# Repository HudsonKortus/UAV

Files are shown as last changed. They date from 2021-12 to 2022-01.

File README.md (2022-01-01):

<div align="center">
    accessibility text
</div>

# UAV 2.0
UAV 2.0 is a thrust vector controlled, electric ducted fan powered UAV. I started this project in June of 2020, and have been working on it off and on ever since. Over the course of this project I have become a better programmer, more confident in CAD, I have learned how to aerodynamically simulate parts in CFD, and taught myself how to make custom PCBs using EAGLE. There is still work that needs to be done to get the UAV to a place where it can fly. 

# ABOUT
The UAV utilizes moveable thrust vanes which are in the exhaust stream of the electric ducted fan to stabilize the vehicle. The control system is a very basic PID loop, but I plan to move to an LQG controller which will allow the UAV to hover in one place. All the electronics are custom. I used a Teensy 4.0 for the microcontroller, and BMI 088 for the gyroscope and acceleration reading. The electric ducted fan is a basic one I got off Amazon which runs off a 4s, 4000mAh lipo. The electric ducted fan produces a little over 1.2kg of static thrust which currently is not enough to lift the vehicle.

# TODO
 * make UAV be tethered to battery instead of carrying it because the battery is too heavy
 * change form using thrust vanes to gimbaling the motor because thrust vanes cannot be practically mathematically characterizes
 * rewrite code to be more object oriented
 * replace the PID controller with an LQG controller
 * make FAA compliant

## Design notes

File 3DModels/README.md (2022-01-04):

# EDF Mount
<div align="float left">
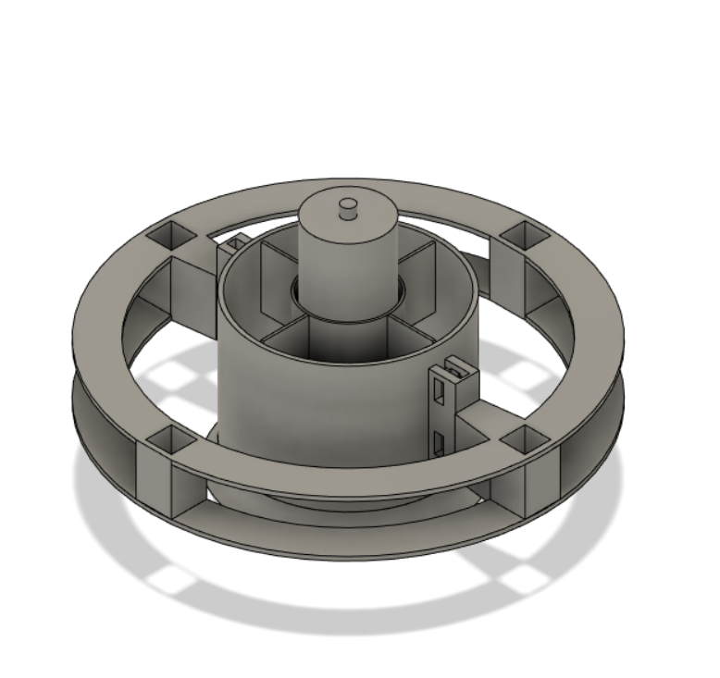
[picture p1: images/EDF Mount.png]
  
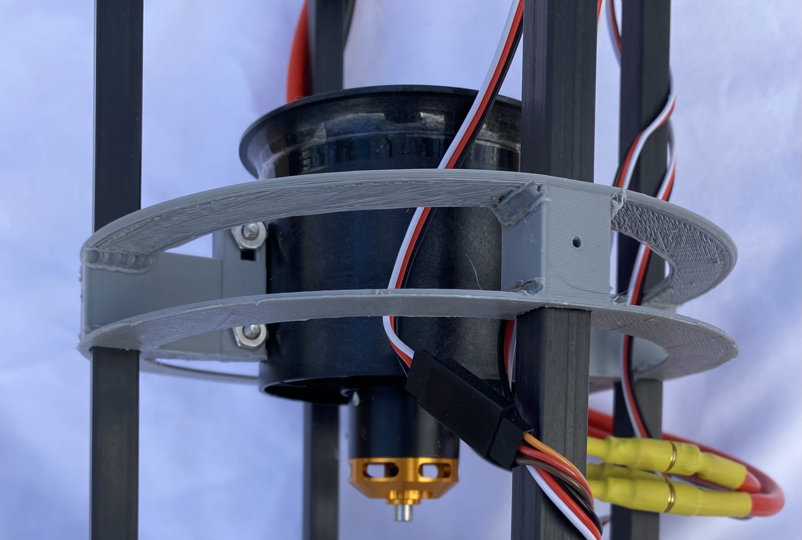
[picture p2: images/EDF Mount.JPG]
  
</div>
This part mounts the electric ducted fan to the carbon fiber frame. I designed this part to be as light as possible which is why there are only 2 thin strips of material connecting each of the frame attachment points. The mount does not need to be rigid in the vertical axis, and just needs to transfer the lift generated by the electric ducted fan to the carbon fiber frame, while ensuring it is rigid horizontally. From my testing, I found that it was unnecessary to have all 4 frame attachment points be fixed to the electric ducted fan, so instead, I only attached the electric ducted fan to 2 of the frame mounting points.

<br/>

# Electronics Disk Mount
<div align="float left">
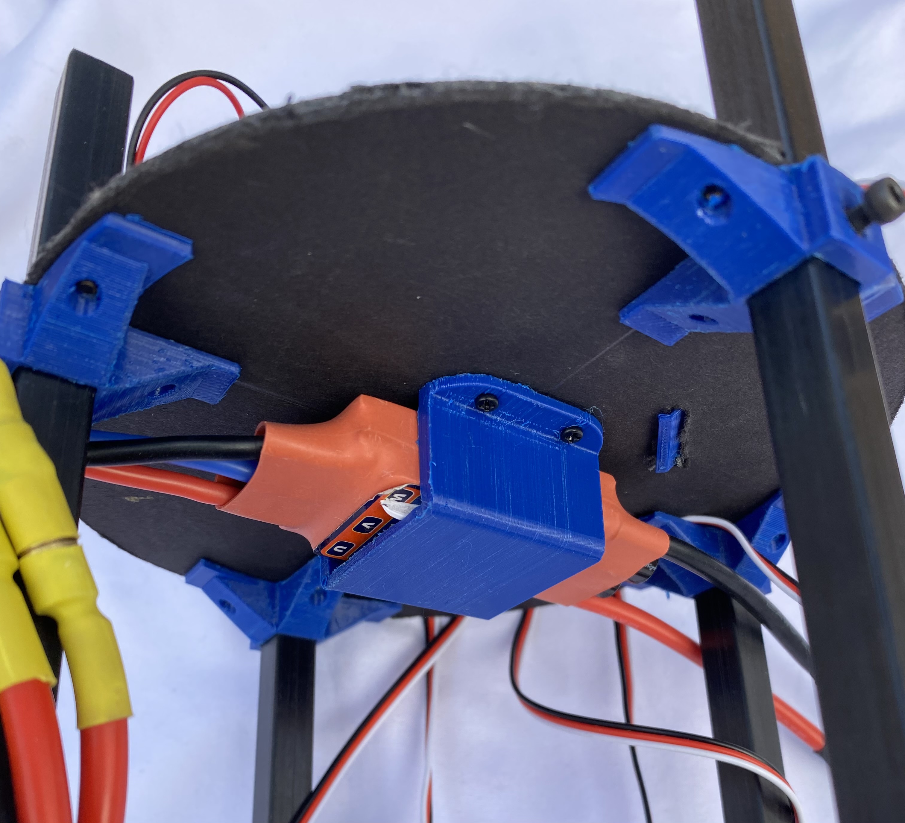
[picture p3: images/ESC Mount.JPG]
  
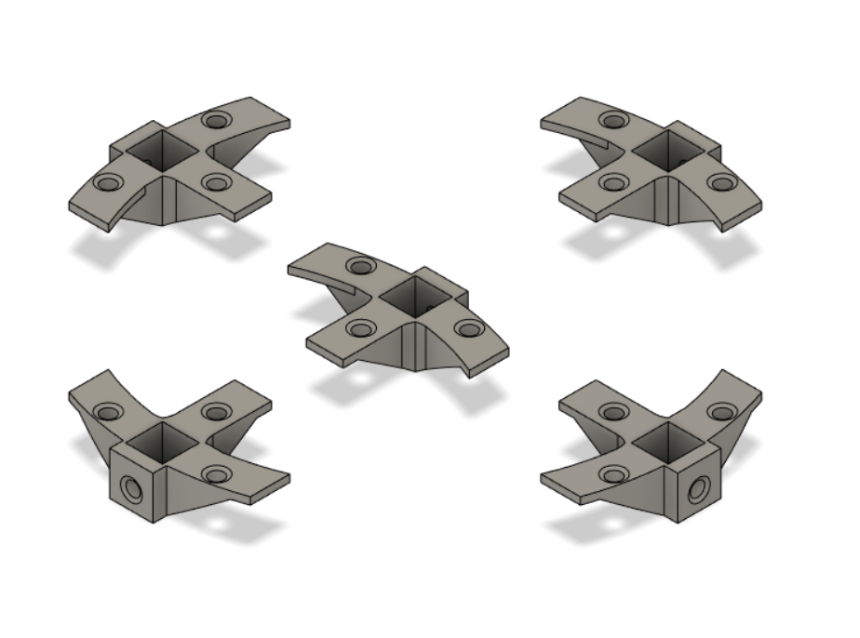
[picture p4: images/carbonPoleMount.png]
  
</div>
 This part is used to affix the foam core disk for the electronics to the carbon fiber mount. The round holes are designed to have threaded inserts mounted in them to allow the foam disk to be screwed in, and to allow the mounts to be screwed to the carbon fiber frame. This file contains all 4 mounts arranged radially and ready to be mounted, as well as a single one which will be easier to 3d print, change, or look at.

<br/>

# ESC Mount
<div align="float left">
  
</div>
This part mounts the 80A ESC to the bottom of the foam core electronics disk. This part is screwed into the foam board with m2 screws.

<br/>

# Gimbal Mount
<div align="float left">
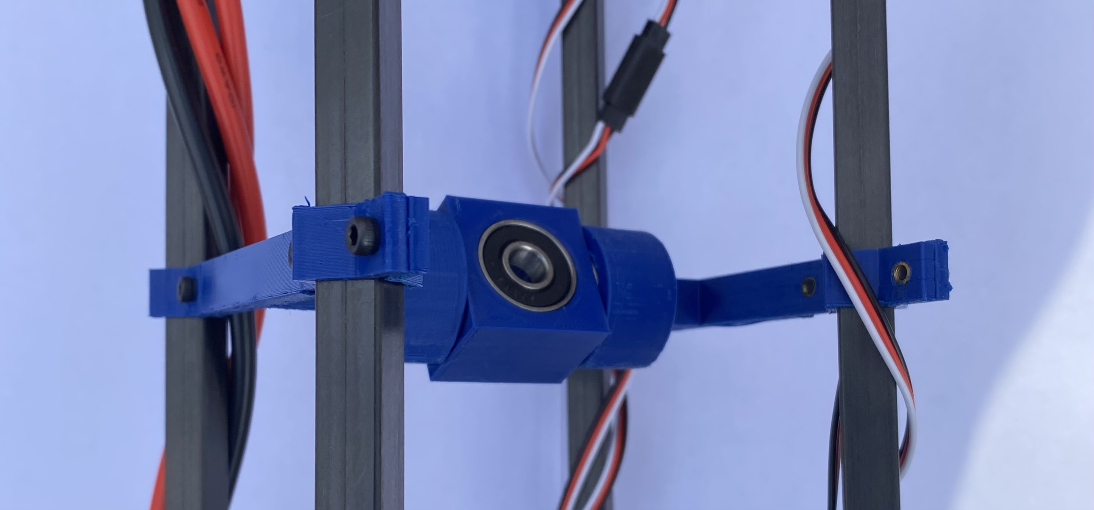
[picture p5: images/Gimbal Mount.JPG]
  
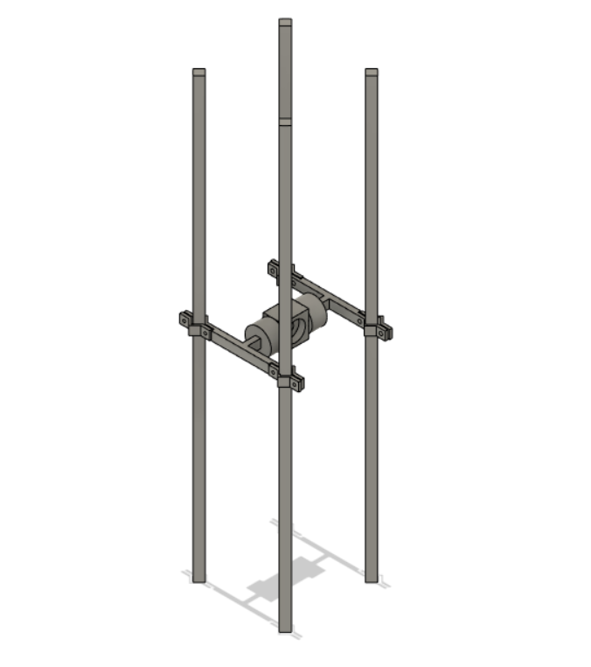
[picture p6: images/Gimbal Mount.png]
  
</div>
This is a two degree of freedom gimbal to allow for the uav to be stationary mounted and tested. It uses threaded inserts and m3 screws to clamp itself to the frame.

<br/>

# Servo Mount
<div align="float left">
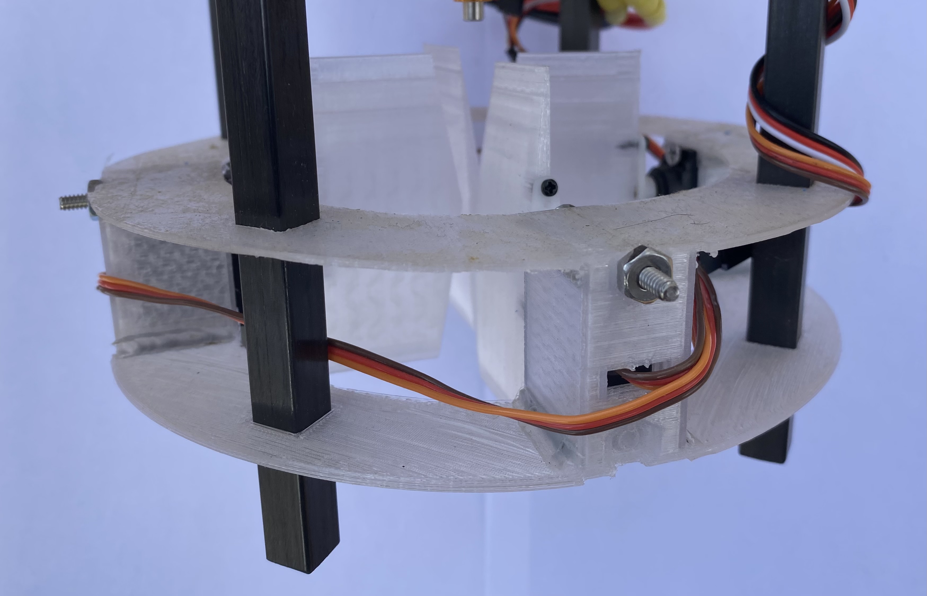
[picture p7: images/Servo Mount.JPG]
  
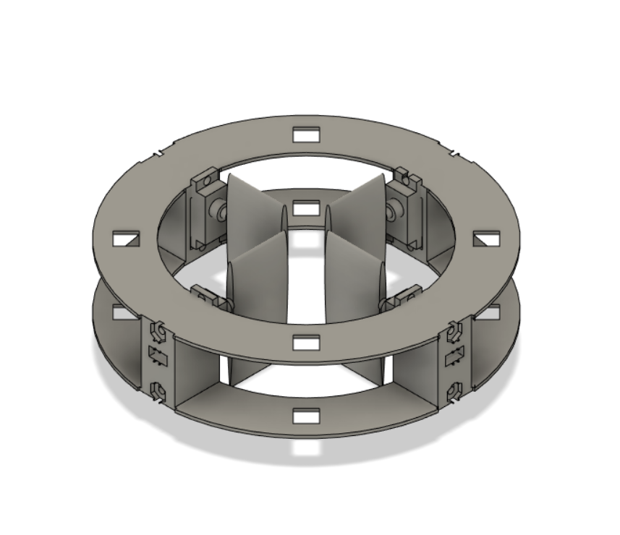
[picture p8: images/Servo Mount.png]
  
</div>
This mounts the servos and thrust vanes to the carbon fiber frame. This part is also extremely optimized to keep the weight down as much as possible.

<br/>

# Thrust Vane
<div align="float left">
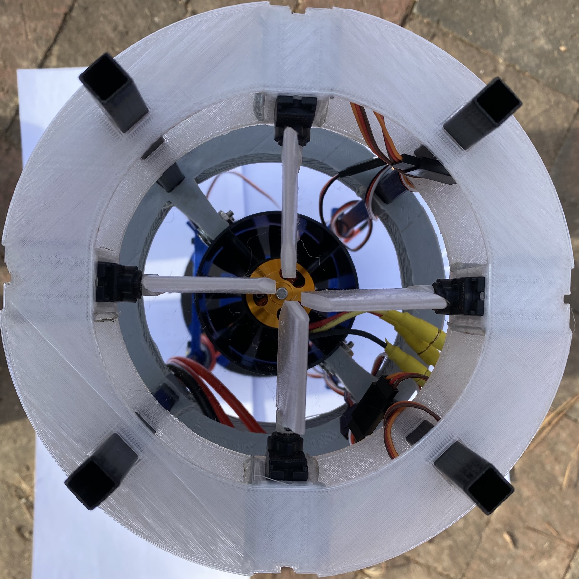
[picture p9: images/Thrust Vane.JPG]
  
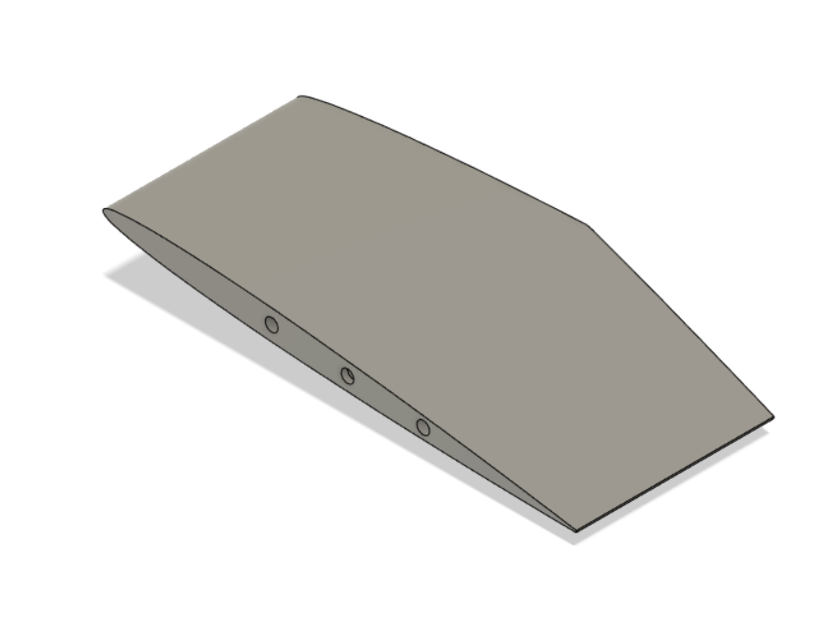
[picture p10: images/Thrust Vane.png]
  
</div>
Thrust vane used to control the UAV.

<br/>

# UAV PCB
<div align="float left">
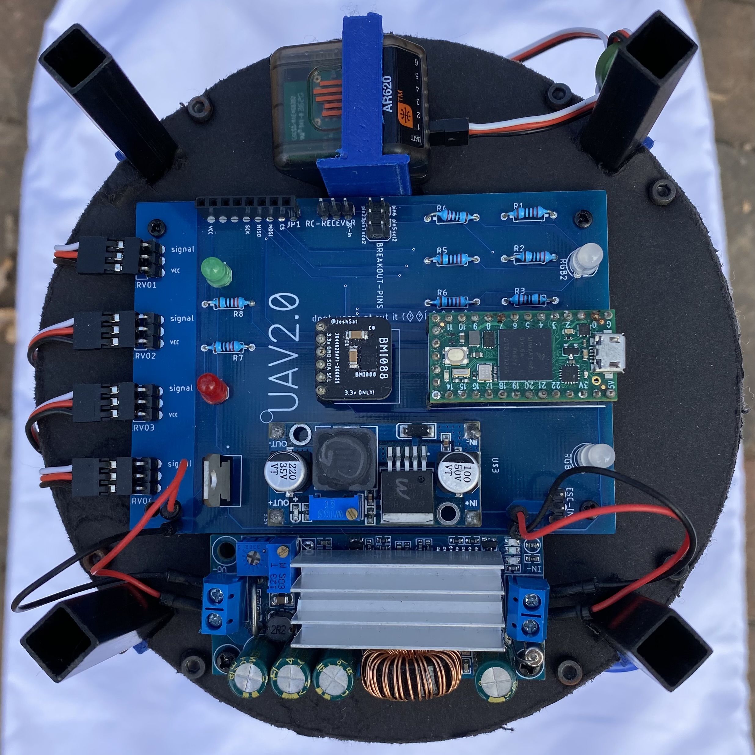
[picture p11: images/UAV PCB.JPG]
  
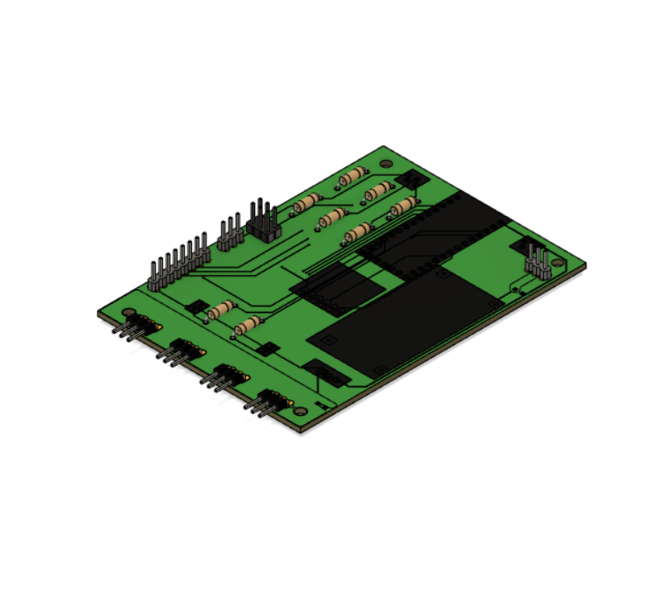
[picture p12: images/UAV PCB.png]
  
</div>
All the necessary data for the PCB used on my UAV is here. Inside the UAV PEB folder is the schematic and board as well as a zip containing all the pertinent information for the PCB to be manufactured.

<br/>

# Receiver Mount
<div align="float left">
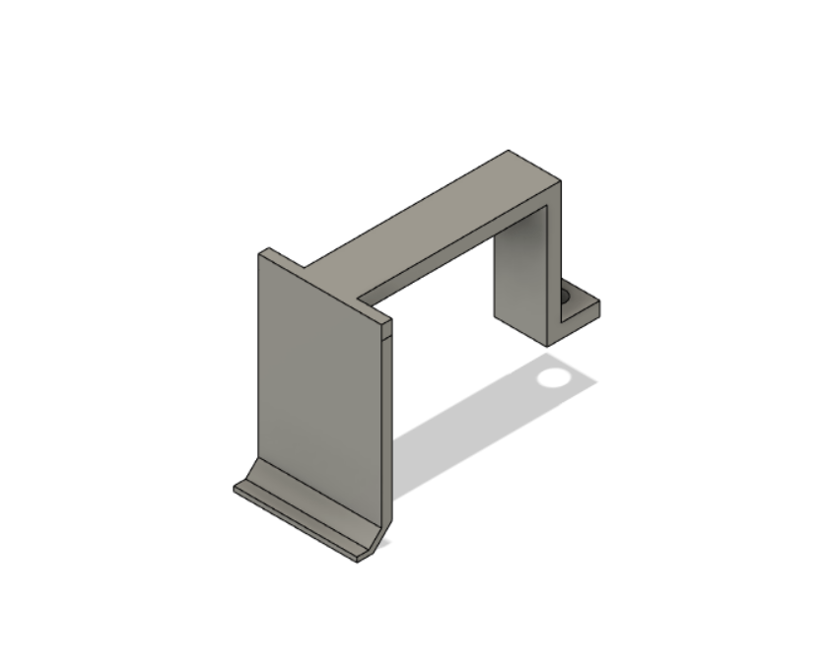
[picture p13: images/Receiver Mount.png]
  
</div>
Mounts the RC receiver to the foam core.

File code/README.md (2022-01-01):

# About
This is the code which runs the UAV. It uses a simple PID loop to determine the amount of torque required to keep the vehicle under control, In order to account for the thrust of the electric ducted fan, I used an equation which calculates the thrust generated by a thrust vane as detailed in <a href="https://smartech.gatech.edu/handle/1853/59935">this paper by Jacob Grey Sobering</a>. Quaternions are used to derive the orientation of the UAV from acceleration measurements. I used a closed source quaternion library, so that code is missing from this repository. If you want to use this code, simply add your own orientation code to the angle_output method. This code is over a year old and since writing it, I have greatly improved in my programming abilities. I will soon rewrite the code to be truly object oriented, more compact, and easier to read.

# TODO
 * rewrite code to be more object oriented
 * replace the PID controller with an LQG controller

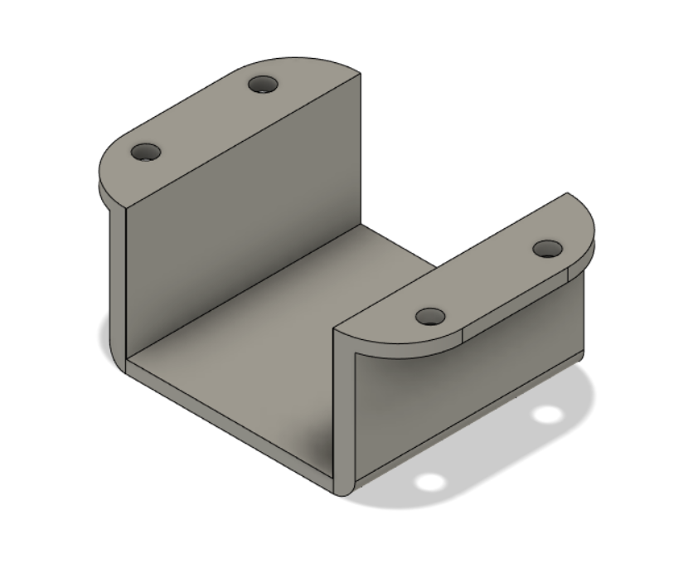
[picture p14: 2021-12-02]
images/ESC Mount.png

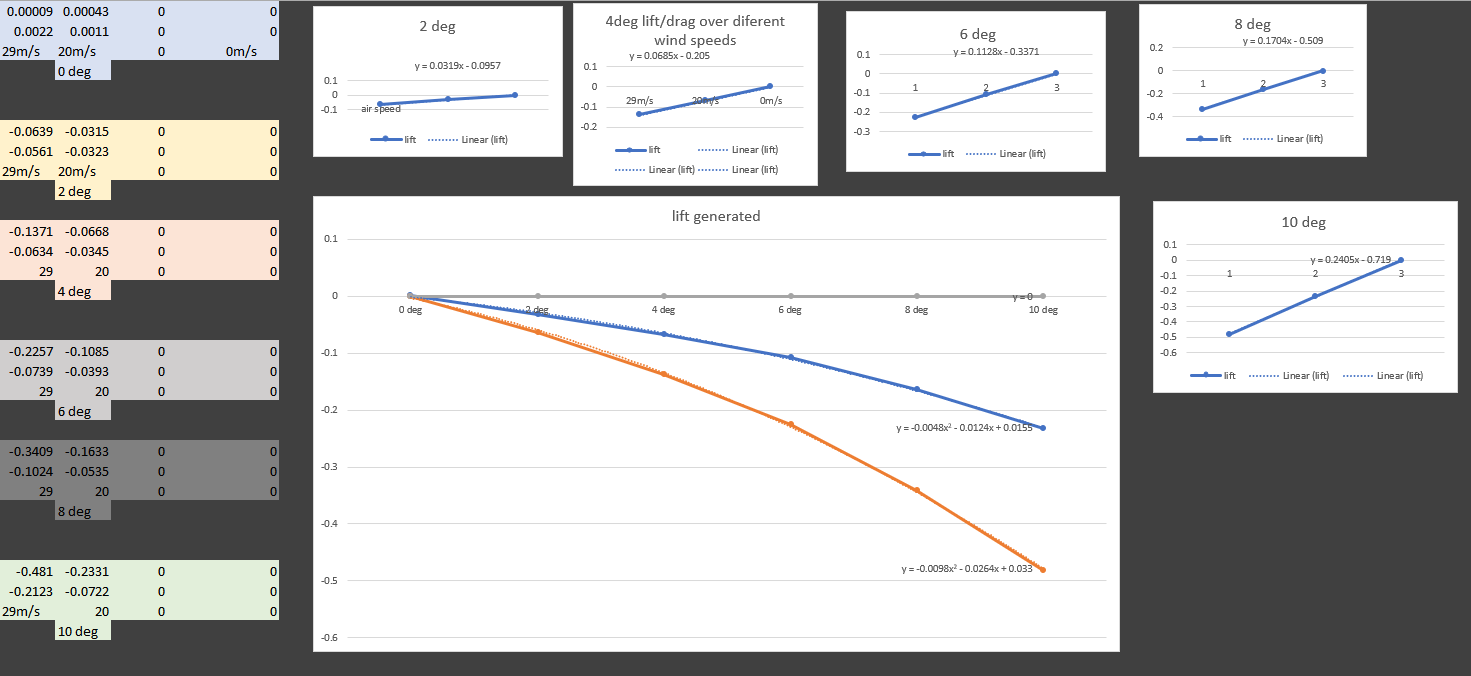
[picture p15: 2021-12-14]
images/Thrust Vane Data.JPG

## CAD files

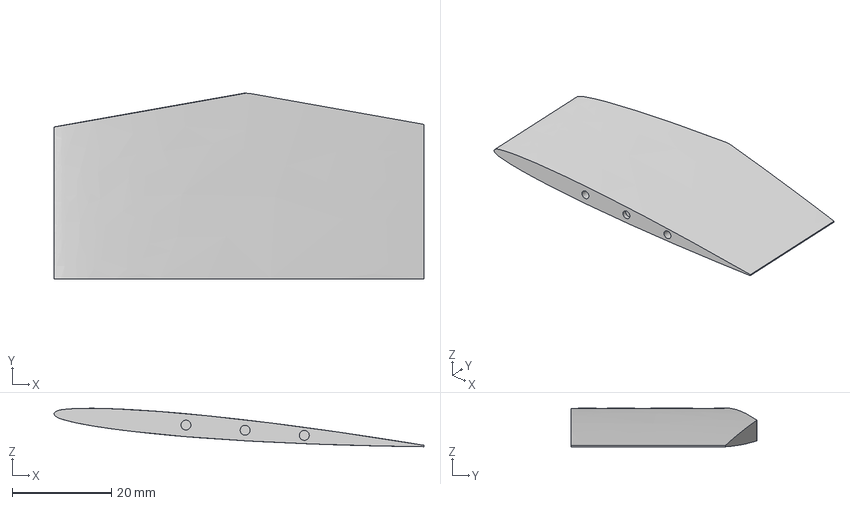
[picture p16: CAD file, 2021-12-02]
3DModels/thrustVane.step
74.7 x 37.5 x 7.78 mm

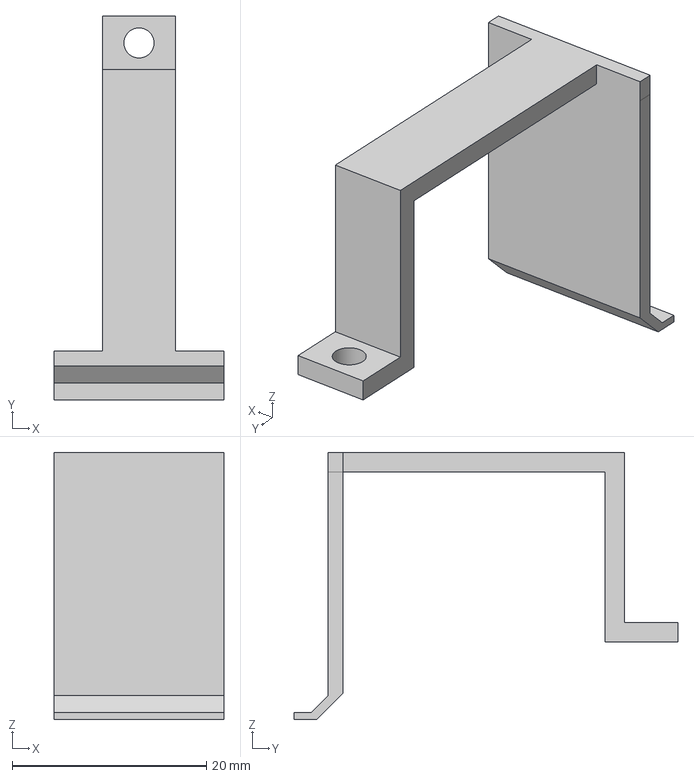
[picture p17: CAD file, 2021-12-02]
3DModels/receverClamp.step
17.5 x 39.5 x 27.5 mm

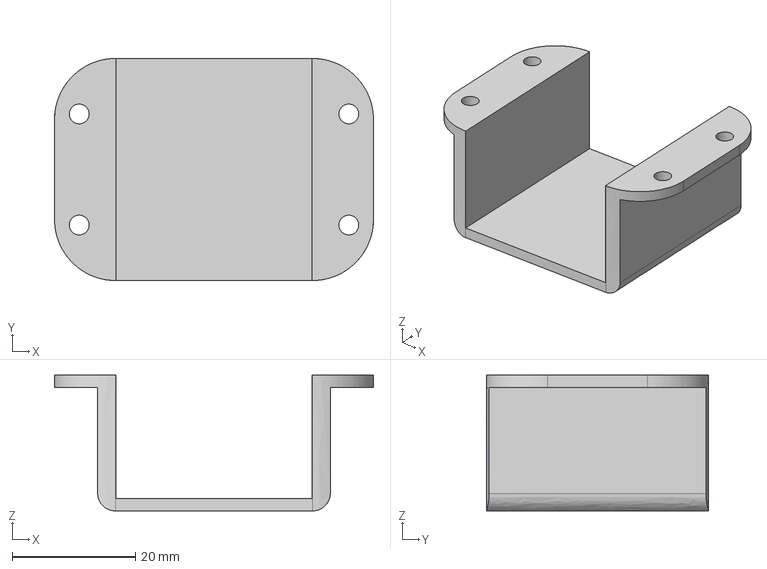
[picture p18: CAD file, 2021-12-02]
3DModels/ESCHolder.step
51.7 x 36.0 x 22.0 mm

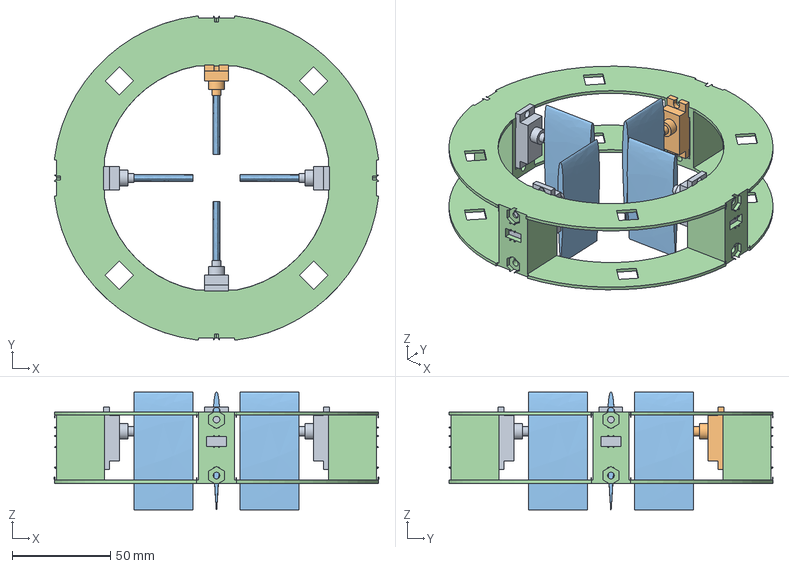
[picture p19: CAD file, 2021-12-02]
3DModels/servoMount.step
165.1 x 165.0 x 60.0 mm
UAVservo v4
thrust vane

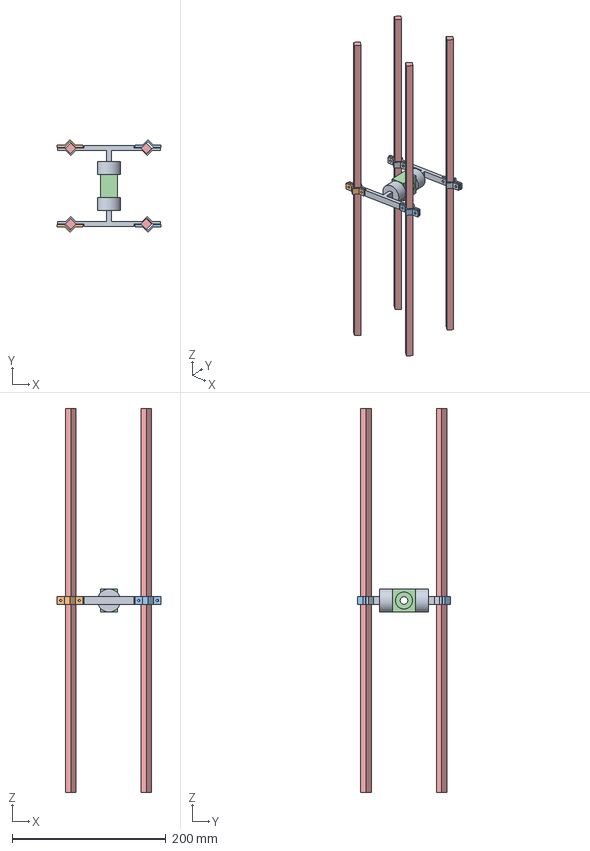
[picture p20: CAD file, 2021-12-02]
3DModels/gimbalForUAV.step
135.8 x 120.6 x 500.0 mm
primary
secondary
main box
CarbonPoles2

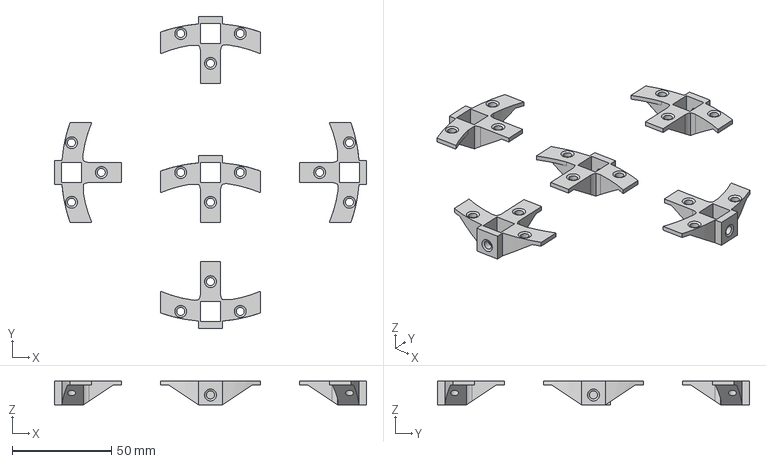
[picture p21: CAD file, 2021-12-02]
3DModels/carbonPoleMount.step
157.2 x 157.2 x 12.0 mm
mount singe x 5

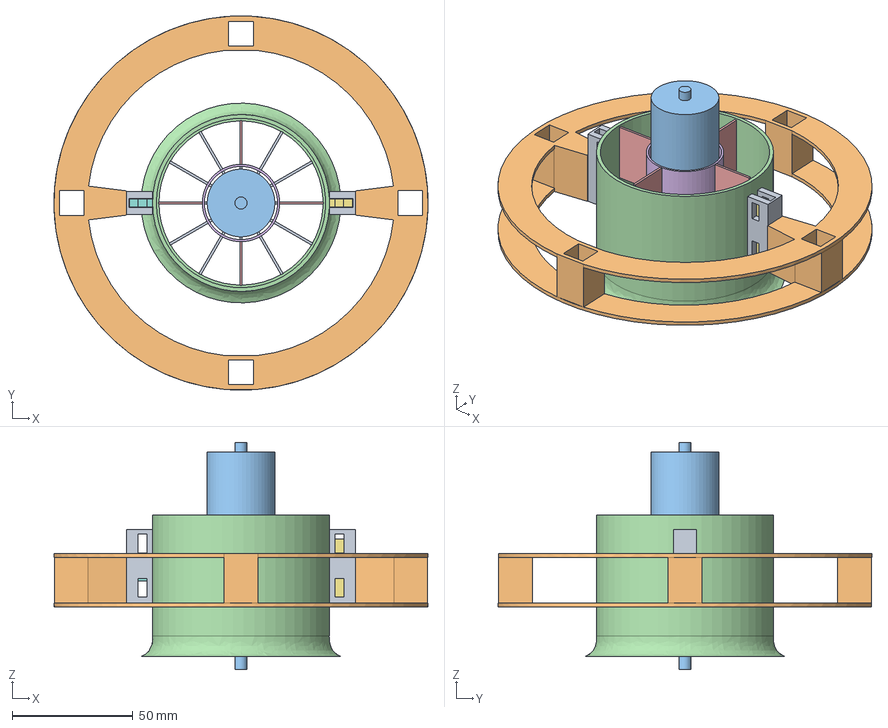
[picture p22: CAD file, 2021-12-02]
3DModels/EDFholder.step
154.6 x 154.6 x 94.0 mm
edfclamp x 2
EDFholder
motor
shroud
blades

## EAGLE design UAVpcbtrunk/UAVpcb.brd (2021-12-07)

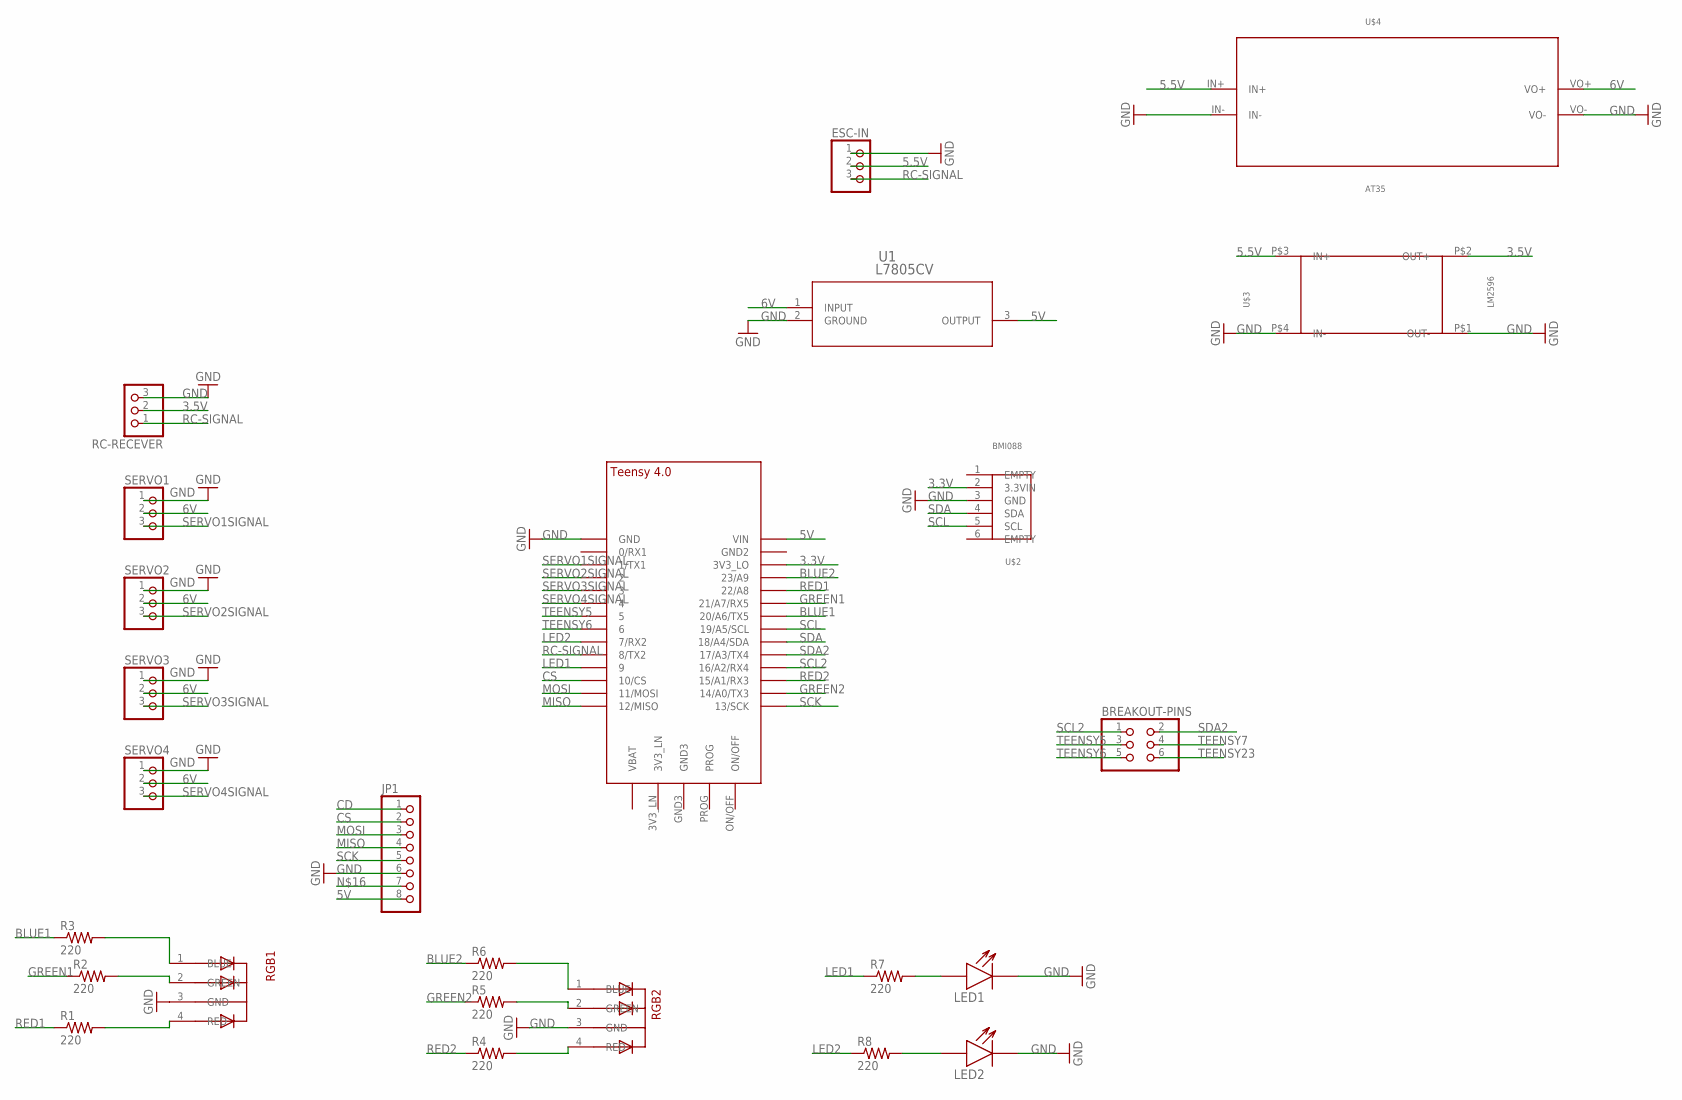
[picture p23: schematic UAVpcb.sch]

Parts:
BREAKOUT-PINS: PINHD-2X3; 2X03
ESC-IN: PINHD-1X3; 1X03
JP1: PINHD-1X8; 1X08
LED1, LED2: LED2P; JP1
R1, R2, R3, R4, R5, R6, R7, R8: 220; 0207/10
RC-RECEVER: PINHD-1X3; 1X03
RGB1, RGB2: 5MMRGBLED; LED5MMRGB
SERVO1, SERVO2, SERVO3, SERVO4: PINHD-1X3/90; 1X03/90
U1: L7805CV; TO-220_STM
U$1: TEENSY_4.0
U$2: BMI088; 1X06
U$3: LM2596
U$4: AT35

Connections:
3.3V: U$1.3V3_LO, U$2.2 (3.3VIN)
3.5V: RC-RECEVER.2, U$3.P$2 (OUT+)
5.5V: ESC-IN.2, U$3.P$3 (IN+), U$4.IN+
5V: JP1.8, U1.3 (OUTPUT), U$1.VIN
6V: SERVO1.2, SERVO2.2, SERVO3.2, SERVO4.2, U1.1 (INPUT), U$4.VO+
BLUE1: R3.1, U$1.20/A6 (20/A6/TX5)
BLUE2: R6.1, U$1.23/A9
CD: JP1.1
CS: JP1.2, U$1.10/CS
GND: ESC-IN.1, JP1.6, LED1.2 (K), LED2.2 (K), RC-RECEVER.3, RGB1.3 (GND), RGB2.3 (GND), SERVO1.1, SERVO2.1, SERVO3.1, SERVO4.1, U1.2 (GROUND), U$1.GND, U$2.3 (GND), U$3.P$1 (OUT-), U$3.P$4 (IN-), U$4.IN-, U$4.VO-
GREEN1: R2.1, U$1.21/A7 (21/A7/RX5)
GREEN2: R5.1, U$1.14/A0 (14/A0/TX3)
LED1: R7.1, U$1.9/CS (9)
LED2: R8.1, U$1.7 (7/RX2)
MISO: JP1.4, U$1.12/MISO
MOSI: JP1.3, U$1.11/MOSI
unnamed: LED1.1 (A), R7.2
unnamed: LED2.1 (A), R8.2
unnamed: R6.2, RGB2.1 (BLUE)
unnamed: R5.2, RGB2.2 (GREEN)
unnamed: R4.2, RGB2.4 (RED)
unnamed: R3.2, RGB1.1 (BLUE)
unnamed: R2.2, RGB1.2 (GREEN)
unnamed: R1.2, RGB1.4 (RED)
RC-SIGNAL: ESC-IN.3, RC-RECEVER.1, U$1.8 (8/TX2)
RED1: R1.1, U$1.22/A8
RED2: R4.1, U$1.15/A1 (15/A1/RX3)
SCK: JP1.5, U$1.13/SCK
SCL: U$1.19/A5/SCL, U$2.5 (SCL)
SCL2: BREAKOUT-PINS.1, U$1.16/A2 (16/A2/RX4)
SDA: U$1.18/A4/SDA, U$2.4 (SDA)
SDA2: BREAKOUT-PINS.2, U$1.17/A3 (17/A3/TX4)
SERVO1SIGNAL: SERVO1.3, U$1.1/TX (1/TX1)
SERVO2SIGNAL: SERVO2.3, U$1.2
SERVO3SIGNAL: SERVO3.3, U$1.3/CANTX (3)
SERVO4SIGNAL: SERVO4.3, U$1.4/CANRX (4)
TEENSY5: BREAKOUT-PINS.3, U$1.5
TEENSY6: BREAKOUT-PINS.5, U$1.6
TEENSY7: BREAKOUT-PINS.4
TEENSY23: BREAKOUT-PINS.6

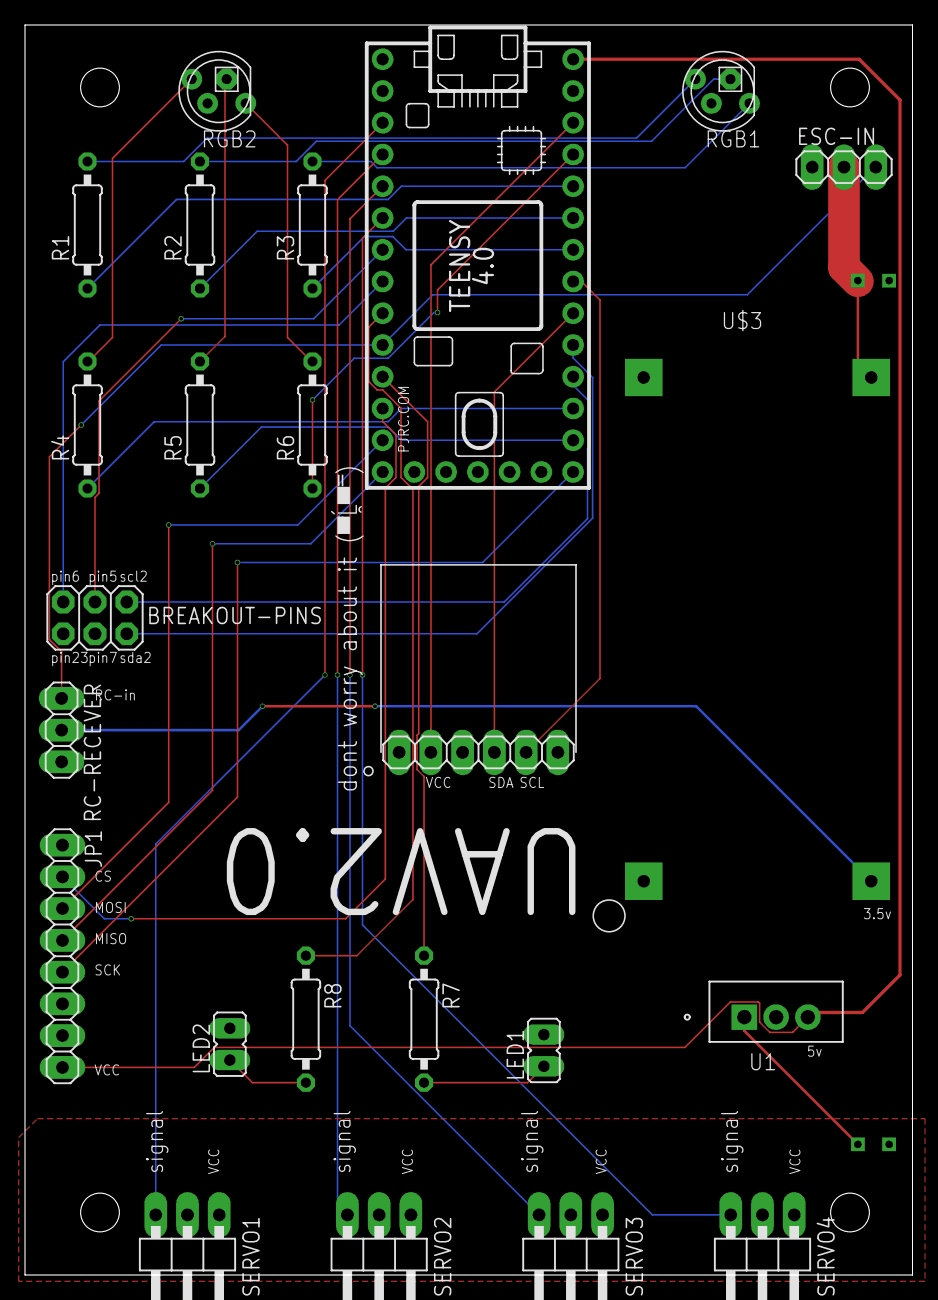
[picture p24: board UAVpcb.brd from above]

Board: 2 copper layers, 71.0 x 100.0 mm, 25 parts (1 on the bottom side), 37 nets.

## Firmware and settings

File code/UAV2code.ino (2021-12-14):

#include <PWMServo.h>
#include "BMI088.h"
#include "Vec3D.h"
#include "Quat.h"
#include "globalVars.h"
#include "PID.h"
/* accel object */
Bmi088Accel accel(Wire,0x18);
/* gyro object */
Bmi088Gyro gyro(Wire,0x68);

PWMServo servo1;//y vane
PWMServo servo2;//z vane
PWMServo servo3;//y vane
PWMServo servo4;//z vane
float runtime;

//unsigned long duration;
//int pin = 7;
//int angle;

Quat base(1.0f, 0.0f, 0.0f, 0.0f);// establishes base of quaternion 

void setup() {
  // put your setup code here, to run once:
  setupGyro();
  servo1.attach(1);
  servo2.attach(2);
  servo3.attach(3);
  servo4.attach(4);
  pinMode(pin1, INPUT);
  pinMode(pin2, INPUT); 
  pinMode(EDFreadPin, INPUT);
  pinMode(warningPin, OUTPUT);
}

void loop() {
  angle_output();
  findEDFthrust(EDFthrust);
  degVaney = PID(Kpy,Kiy,Kdy,pitch,desiredAngley);
  degVanez = PID(Kpz,Kiz,Kdz,yaw,desiredAnglez); 

  Serial.println("thrust");
  Serial.println(thrust);
  Serial.println("degVaney");
  Serial.println(degVaney); 
  Serial.println("degVanez");
  Serial.println(degVanez);
  Serial.println(" ");
  intagrateServos();
  
}

void intagrateServos() {
  
  servoValX = degVaney/numYvanes;
  servoValZ = degVanez/numZvanes;
  /*
                               <X>
                              servo1[pin 8]
                                |
                ^               |                ^
                Z  servo4  ----- O ----- servo 2  Z[pin 6]
                v    [pin4]     |                v
                                |
                           servo 3 [pin 5]
                               <X>
                                  
  */
  
  //adds togeather all servo values
  servoVal1 = (-servoValX) + 90;
  servoVal2 = (-servoValZ) + 90;
  servoVal3 = (servoValX) + 90;
  servoVal4 = (servoValZ) +  90;

  //prevent thrust vanes from hitting each other
  servoVal1 = constrain ( servoVal1, 80, 110);
  servoVal2 = constrain ( servoVal2, 80, 110);
  servoVal3 = constrain ( servoVal3, 80, 110);
  servoVal4 = constrain ( servoVal4, 80, 110);

  Serial.println("servoVal1");
  Serial.println(servoVal1); 
  Serial.println("servoVal2");
  Serial.println(servoVal2);

  //tells servos to do
  servo1.write(servoVal1);
  servo2.write(servoVal2);
  servo3.write(servoVal3);
  servo4.write(servoVal4);



  
}

void setupGyro(){
//    timeLast = micros();
  int status;
  /* USB Serial to print data */
  Serial.begin(115200);
  while(!Serial) {}
  /* start the sensors */
 
  status = gyro.begin();
  if (status < 0) {
    Serial.println("Gyro Initialization Error");
    Serial.println(status);
    while (1) {}
  }
}

void angle_output() { 
   //set the derivative quaternion- set how fast our base quaternion is changing
  Quat q_half = base / 2.0f; 
  Vec3D gyro = getGyro();
  current_time = micros(); //gets our time between last loop
  dt = current_time - previous_time; //gets  our time between last loop
  dt = dt / 1000000.0f; //gets our time between last loop
  //make sure gyro is in radians!!!!!!!
  Quat q_dot = q_half.derivative(gyro); //sets the derivative quaternion based on the gyro rates (gyro must be vector)
  Quat q_int = q_dot.integrate(dt);
  base += q_int; //adds the change in quaternion orientation to the current quaternion orientation so we can track it over time
  ypr = base.toEuler();//converts our base quaternion (the one tracking our orientation) to nice easy to read euler angles
  //TODO: make this work
  //ypr.toDegrees();
  previous_time = current_time;
  //Serial.println (ypr.toDegrees());
  //Serial.println ("ypr.x");
  //Serial.println (ypr.toDegrees().z);
  yaw = ypr.z;
  pitch = ypr.y;
  roll = ypr.x;
  Serial.println("yaw");
  Serial.println(ypr.toDegrees().z,7);
  Serial.println("pitch");
  Serial.println(ypr.toDegrees().y,7);
}

Vec3D getGyro() {
   gyro.readSensor();
   Vec3D gyros(gyro.getGyroX_rads(),gyro.getGyroY_rads(),gyro.getGyroZ_rads());
  // Serial.println ("gyro.getGyroX_rads()");
   //Serial.println (gyro.getGyroX_rads());
   return gyros;
}

int findEDFthrust(int EDFthrust){

  EDFduration = pulseIn(EDFreadPin, HIGH);
  thrust = map (EDFduration, 900, 2000, 0, 1100);
  thrust = constrain (thrust, 100, 1000);

  return thrust;
}

 

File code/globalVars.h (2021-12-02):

#pragma once

//UAV parameters
int edfArea = 38;//edf area
int vaneSA = 23; //vane surface area
int thrust = 900; //the amount of thrust at any given %
float SA = 1.21; //ratio of vane survace area to edf area
float Dcp = 2;//distance betuene cp and center of rotation times Dcp
int EDFmaxThrust = 1100;//max thrust of EDF
int numYvanes = 2; //number of vanes that will influiance pich
int numZvanes = 2; //number of vanes that will influiance yaw
int numXvanes = 4;

//for PID loop
float Kpz = 650;
float Kiz = 0;
float Kdz = 100;
float Xr;//x raw
float Yr;//y raw
float Zr;//z raw
float Kpy = 650;
float Kiy = 0;
float Kdy = 100;

// for servo/ servo intagration
float servoValX; 
float servoValZ;
float servoValY;
float servoVal1;// the pwm or deg value for each servo
float servoVal2;// the pwm or deg value for each servo
float servoVal3;// the pwm or deg value for each servo
float servoVal4;// the pwm or deg value for each servo
float servoVal1Offset = 94;
float servoVal2Offset = 88;
float servoVal3Offset = 87;
float servoVal4Offset = 98;

//for orentaion
float yaw;// final orentation
float pitch;// final orentation
float roll;// final orentation
float degVaney;
float degVanex;
float degVanez;
float desiredAngley = 0;// the angle that the PID loop will try to keep
float desiredAnglez = 0;// the angle that the PID loop will try to keep
float desiredAnglex = 0;// the angle that the PID loop will try to keep
float angle1;

float angle2;


//time
float current_time = 0.0f;
float previous_time = 0.0f;
Vec3D ypr; // this represents the yaw pitch and roll of the rocket
float dt = 0.0f;
unsigned long duration1;
unsigned long duration2;

//pins
int pin1 = 1;
int pin2 = 2;
int warningPin = 13;

//for findEDFthrust
int EDFreadPin = 8;
unsigned long EDFduration;
int EDFthrust = 900;

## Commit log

2021-12-07 added more pictures and updated the README for 3DModels to be more helpfull
    [UAVpcb.brd, UAVpcb.sch]
2021-12-14 expaded readme files, added image of thrust vane data, and updated thrust vane spreadsheet to make everything easier to read
    [thrustVaneLift.xlsx]
2022-01-01 Removed unnecessary directory containing thrust vane CFD and edited 3D model's readme.
    [2deg.csv, thrustVaneCFD v3.step, thrustVaneCFD-5deg.f3z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]
2022-04-01 add pcb files
    [UAVpcb.brd, UAVpcb.sch]
